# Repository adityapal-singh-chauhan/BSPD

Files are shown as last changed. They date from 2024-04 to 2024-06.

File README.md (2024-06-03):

<H1>BSPD - Brake System Plausibiltiy Device</H1>  
<BR /><H3>
A non - programmable brake, accelerator plausibility circuit.<BR />
Built for FSAE, according to Formula Bharat specs 2024.<BR /></H3>
<ul>
	<li>It feautes upper and lower thresholds for fault detection</li>
	<li>Disconnection or damage to sensor will also trigger the circuit.</li>
  <li>acc/brake_upper_trig - potentiometer sets the sensors output voltage trigger threshold.</li>
  <li>acc/brake_lower_trig - potentiometer sets the minimum volatage output of the sensor.</li>
  <li>The timing for 500ms wait and 10s shutdown can also be fine tuned.</li> 
	<li>onboard volatge regulation(input 15v - 5.5v)</li>
</ul>

BSPD

SCHEMATIC

schematic

PCB layout
PCB

LTspice sim:
all signals
red - fault signal<BR />
green - 500ms wait<BR />
blue - shutdown trigger<BR />

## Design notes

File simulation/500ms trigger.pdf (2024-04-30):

0s | 2s | 4s | 6s | 8s | 10s | 12s | 14s

0.0V

0.5V

1.0V

1.5V

2.0V

2.5V

3.0V

3.5V

4.0V

4.5V

5.0V

5.5V

V(n005)

### --- C:\Users\adity\Documents\fateh\BSPD\BSPD\comp_sim.raw ---

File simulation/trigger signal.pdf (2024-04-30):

0s | 2s | 4s | 6s | 8s | 10s | 12s | 14s

-0.5V

0.0V

0.5V

1.0V

1.5V

2.0V

2.5V

3.0V

3.5V

4.0V

4.5V

5.0V

V(n002)

### --- C:\Users\adity\Documents\fateh\BSPD\BSPD\comp_sim.raw ---

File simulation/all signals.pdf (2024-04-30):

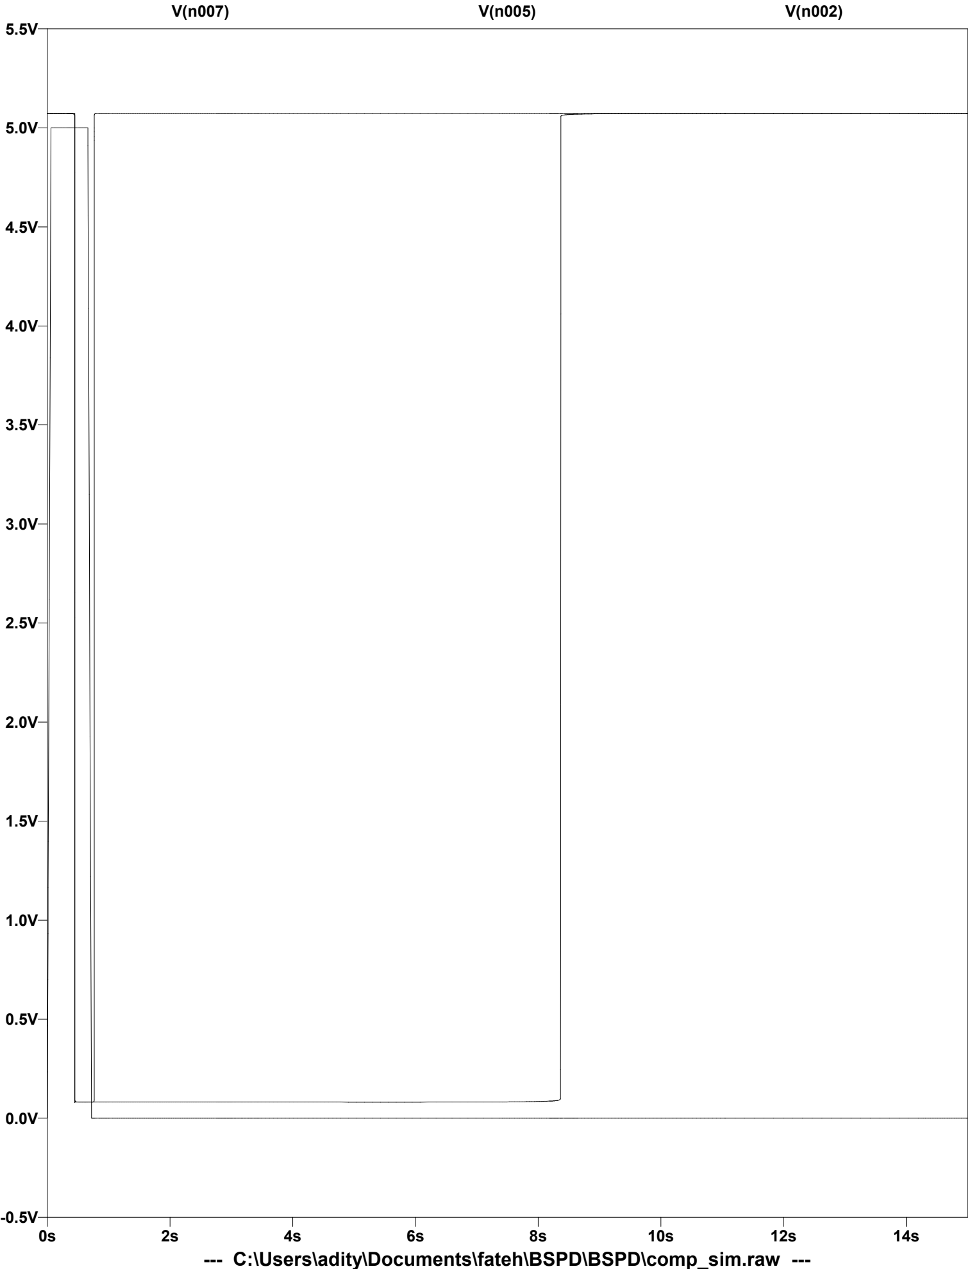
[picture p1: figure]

### --- C:\Users\adity\Documents\fateh\BSPD\BSPD\comp_sim.raw ---

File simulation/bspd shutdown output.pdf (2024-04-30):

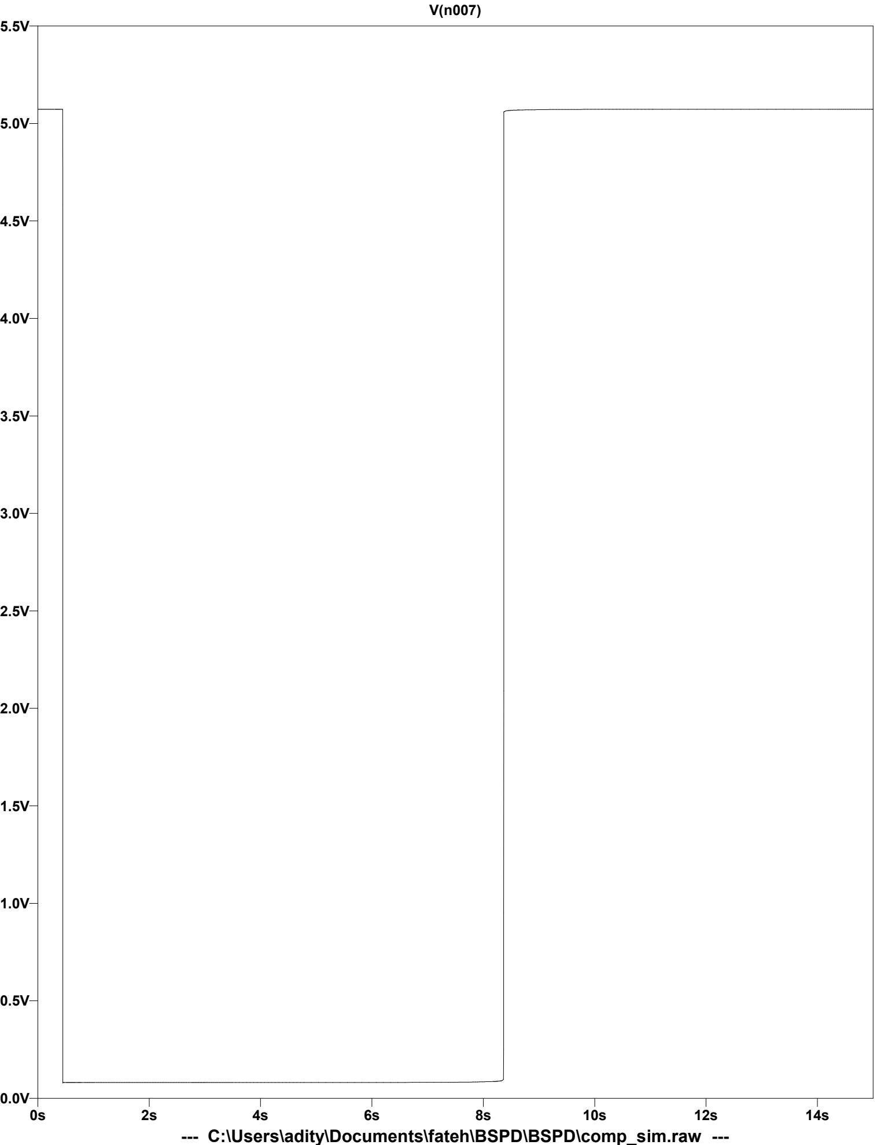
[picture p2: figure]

### --- C:\Users\adity\Documents\fateh\BSPD\BSPD\comp_sim.raw ---

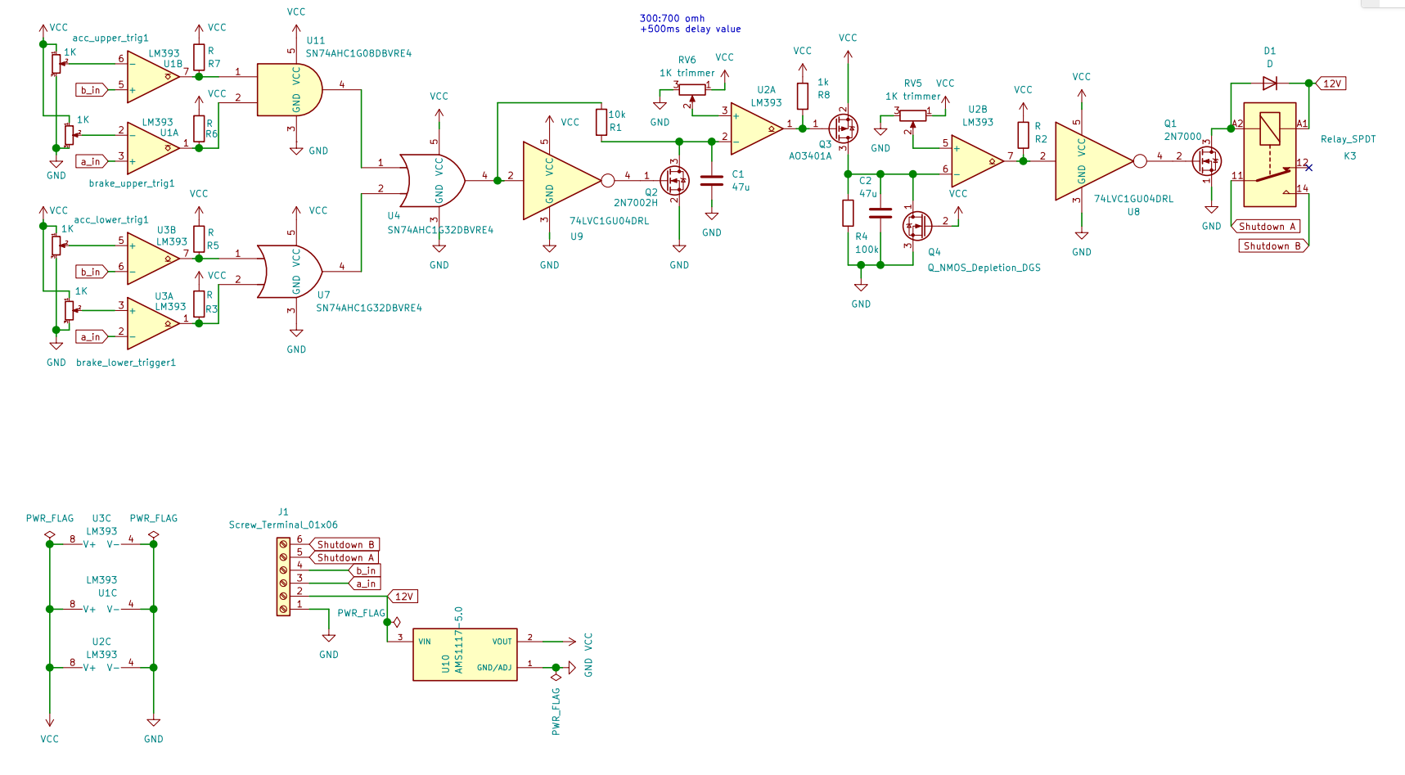
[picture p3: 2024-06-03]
schematic.png

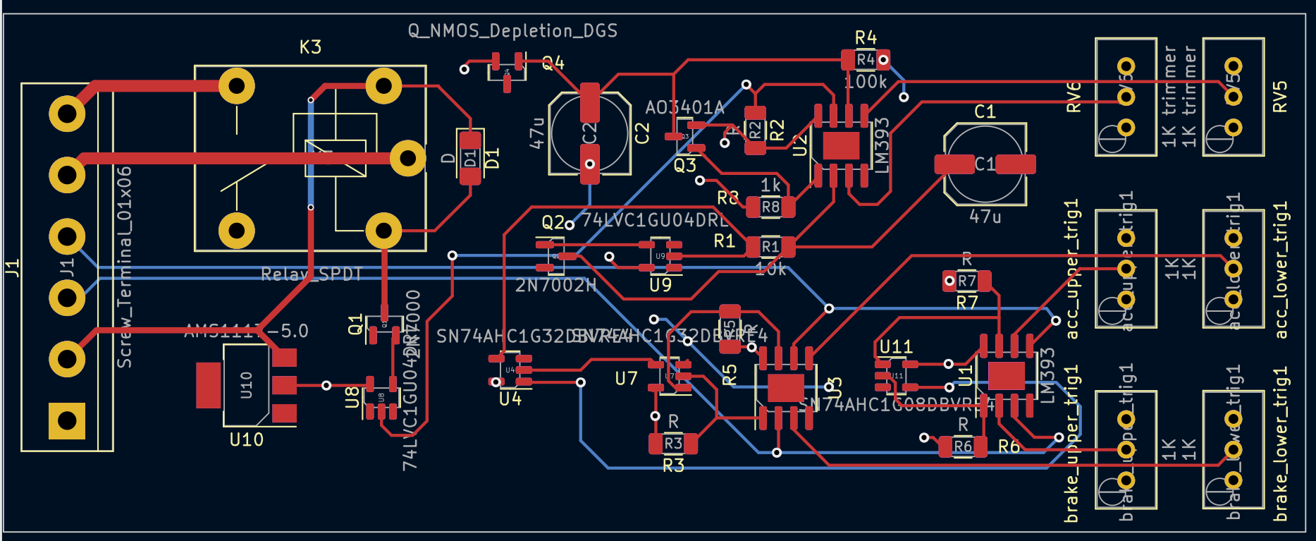
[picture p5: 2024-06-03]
PCB.png

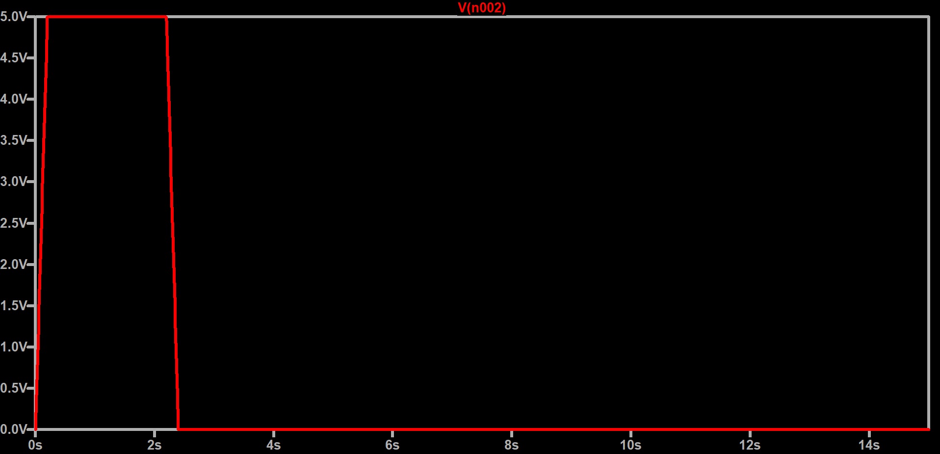
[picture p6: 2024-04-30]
simulation/trigger signal.jpg

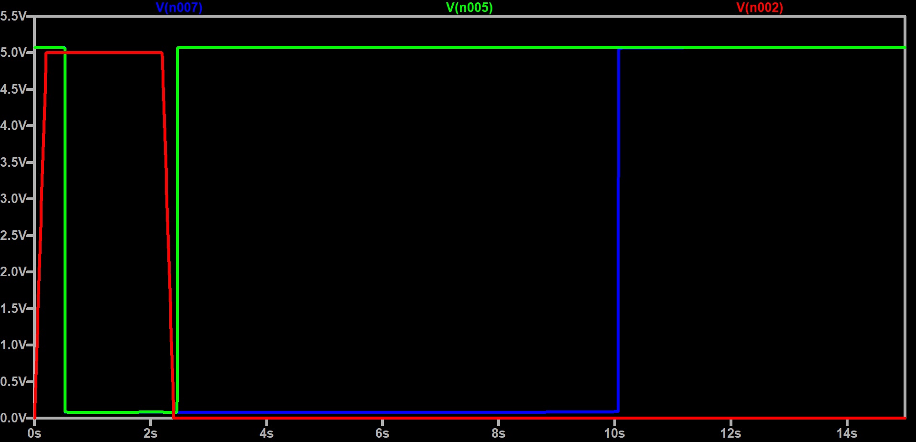
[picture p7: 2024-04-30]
simulation/all signals.jpg

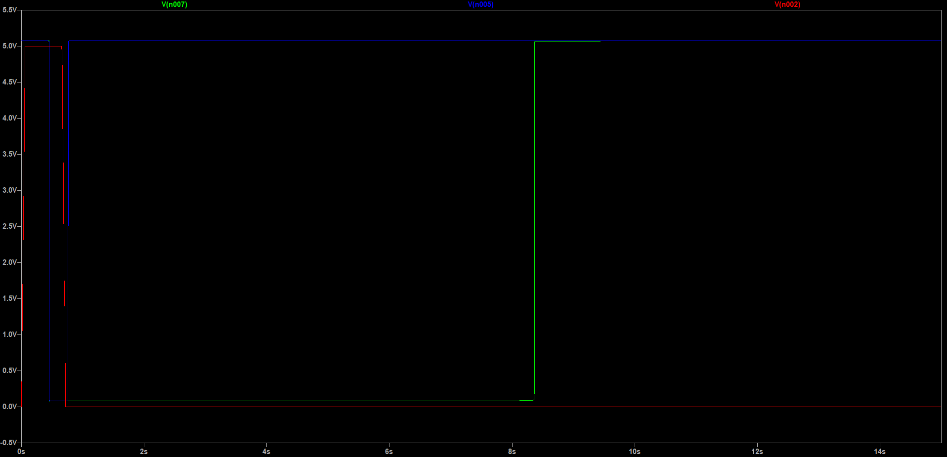
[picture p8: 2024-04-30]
simulation/all signals.png

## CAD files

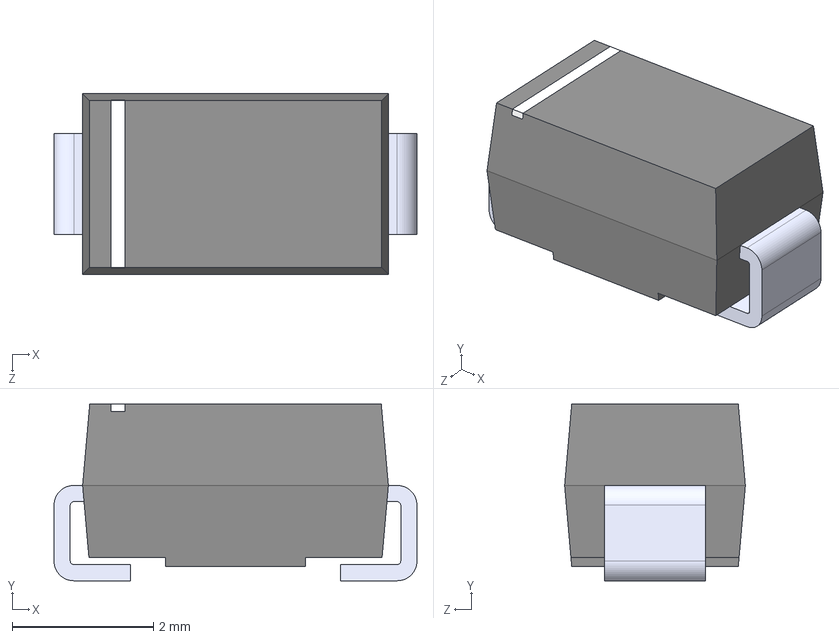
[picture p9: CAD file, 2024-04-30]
1n4007_smd/RS1G.step
5.14 x 2.50 x 2.56 mm

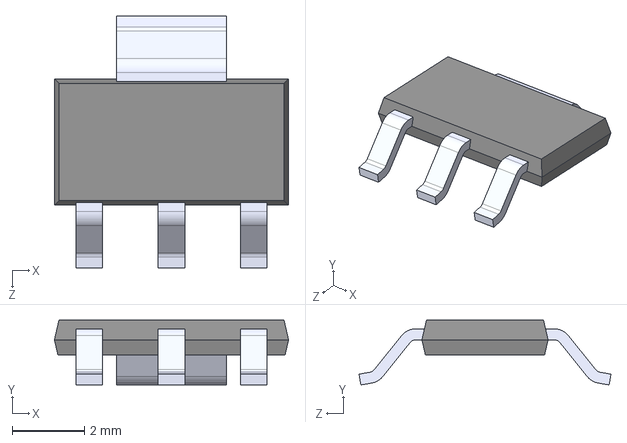
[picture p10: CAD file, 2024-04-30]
AMS1117-5.0/AMS1117-5.0.step
6.50 x 1.80 x 7.00 mm

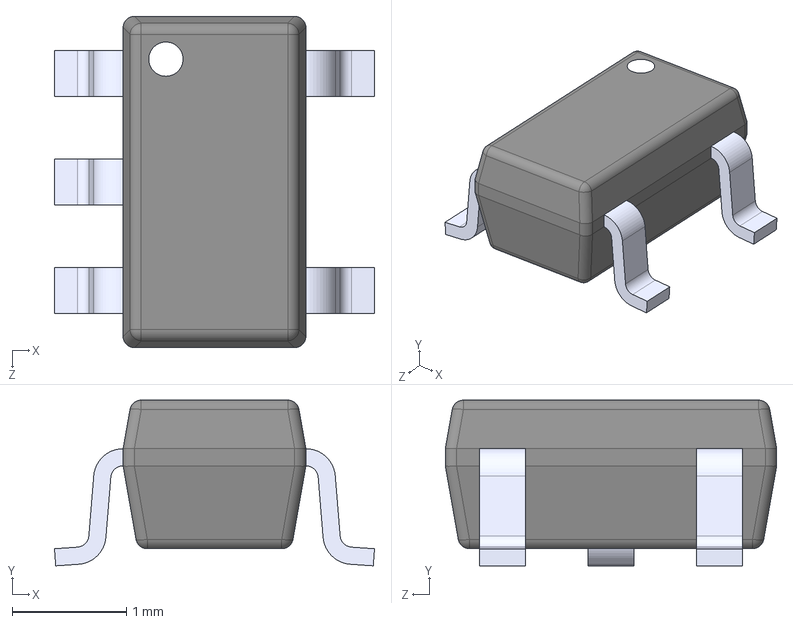
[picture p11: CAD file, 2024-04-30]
SN74AHC1G08DBVRE4/SN74AHC1G08DBVRE4.step
2.80 x 1.45 x 2.90 mm

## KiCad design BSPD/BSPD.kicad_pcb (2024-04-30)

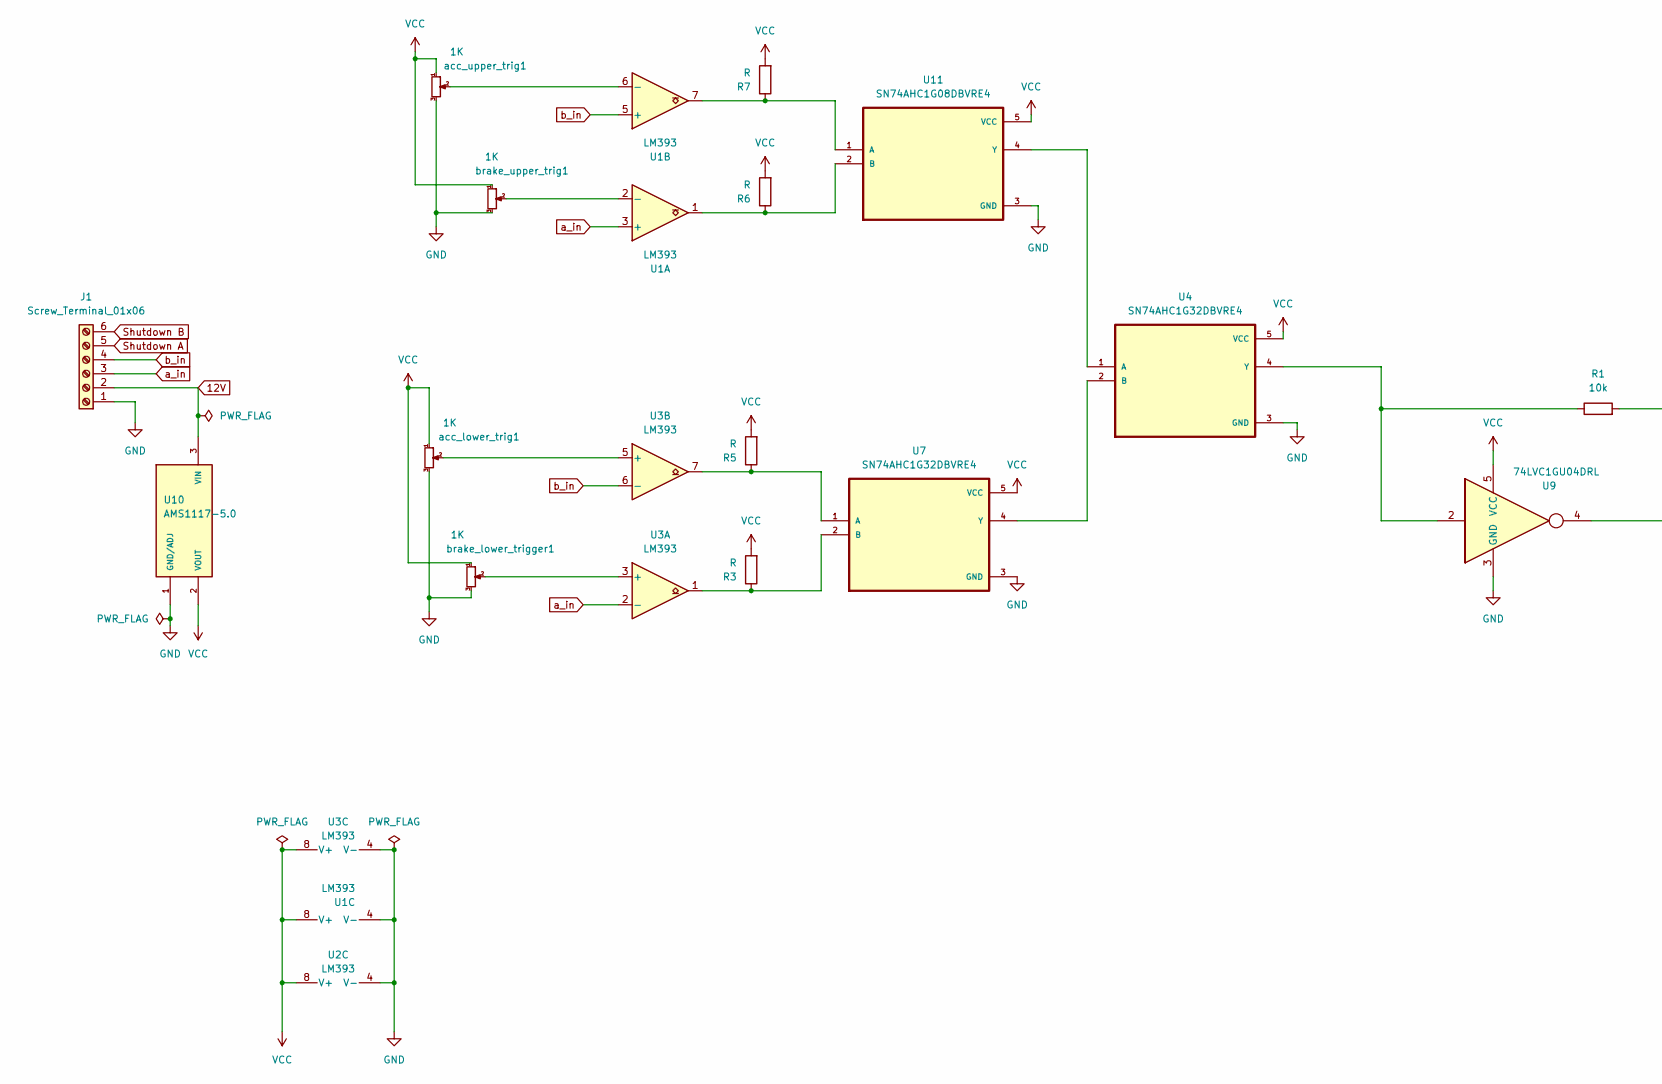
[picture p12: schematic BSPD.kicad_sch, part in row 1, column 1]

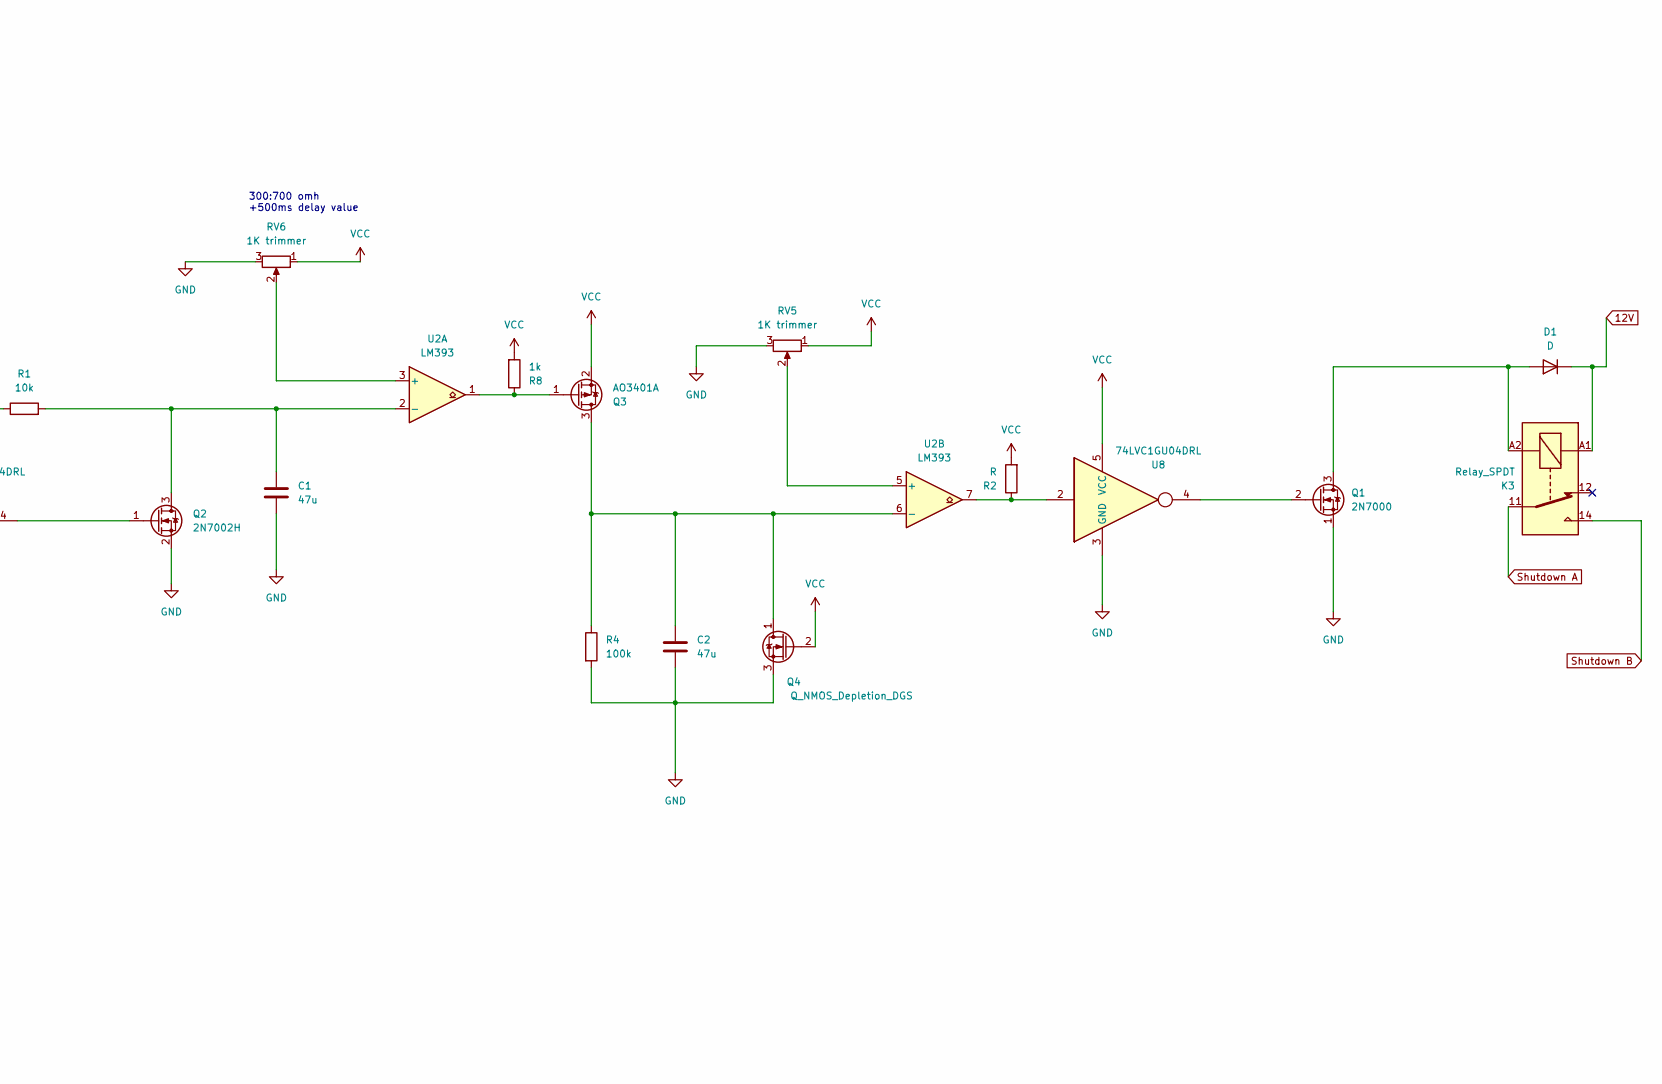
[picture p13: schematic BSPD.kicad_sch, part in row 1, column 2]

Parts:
C1, C2: 47u; C_Elec_6.3x7.7
D1: D; D_1206_3216Metric_Pad1.42x1.75mm_HandSolder
J1: Screw_Terminal_01x06; TerminalBlock_bornier-6_P5.08mm
K3: Relay_SPDT; Relay_SPDT_Finder_36.11
Q1: 2N7000; SOT-23
Q2: 2N7002H; SOT-23
Q3: AO3401A; SOT-23
Q4: Q_NMOS_Depletion_DGS; SOT-23
R1: 10k; R_1206_3216Metric
R2, R3, R5, R6, R7: R; R_1206_3216Metric
R4: 100k; R_1206_3216Metric
R8: 1k; R_1206_3216Metric
RV5, RV6: 1K trimmer; Potentiometer_Bourns_3296W_Vertical
U1, U2, U3: LM393; SOIC-8-1EP_3.9x4.9mm_P1.27mm_EP2.29x3mm
U4, U7: SN74AHC1G32DBVRE4; SOT-23-5
U8, U9: 74LVC1GU04DRL; SOT-23-5
U10: AMS1117-5.0; SOT-223; PARTREV N/A
U11: SN74AHC1G08DBVRE4; SOT-23-5
acc_lower_trig1: 1K; Potentiometer_Bourns_3296W_Vertical
acc_upper_trig1: 1K; Potentiometer_Bourns_3296W_Vertical
brake_lower_trigger1: 1K; Potentiometer_Bourns_3296W_Vertical
brake_upper_trig1: 1K; Potentiometer_Bourns_3296W_Vertical

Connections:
12V: D1.1 (K), J1.2, K3.A1, U10.3 (VIN)
GND: C1.2, C2.2, J1.1, Q1.1 (S), Q2.2 (S), Q4.3 (S), R4.2, RV5.3, RV6.3, U1.4 (V-), U2.4 (V-), U3.4 (V-), U4.3 (GND), U7.3 (GND), U8.3 (GND), U9.3 (GND), U10.1 (GND/ADJ), U11.3 (GND), acc_lower_trig1.3, acc_upper_trig1.3, brake_lower_trigger1.3, brake_upper_trig1.3; also elsewhere on the board
unnamed: D1.2 (A), K3.A2, Q1.3 (D)
unnamed: Q1.2 (G), U8.4
unnamed: C1.1, Q2.3 (D), R1.2, U2.2 (-)
unnamed: Q2.1 (G), U9.4
unnamed: C2.1, Q3.3 (D), Q4.1 (D), R4.1, U2.6 (-)
unnamed: Q3.1 (G), R8.1, U2.1
unnamed: R2.1, U2.7, U8.2
unnamed: U1.2 (-), brake_upper_trig1.2
unnamed: U1.6 (-), acc_upper_trig1.2
unnamed: RV6.2, U2.3 (+)
unnamed: RV5.2, U2.5 (+)
unnamed 13: U3.3 (+), brake_lower_trigger1.2; also elsewhere on the board
unnamed: U3.5 (+), acc_lower_trig1.2
unnamed: U4.2 (B), U7.4 (Y)
unnamed: R1.1, U4.4 (Y), U9.2
unnamed: R5.1, U3.7, U7.1 (A)
unnamed: R3.1, U3.1, U7.2 (B)
unnamed: R7.1, U1.7, U11.1 (A)
unnamed: R6.1, U1.1, U11.2 (B)
unnamed: U4.1 (A), U11.4 (Y)
Shutdown A: J1.5, K3.11
Shutdown B: J1.6, K3.14
VCC: Q3.2 (S), Q4.2 (G), R2.2, R3.2, R5.2, R6.2, R7.2, R8.2, RV5.1, RV6.1, U1.8 (V+), U2.8 (V+), U3.8 (V+), U4.5 (VCC), U7.5 (VCC), U8.5 (VCC), U9.5 (VCC), U10.2 (VOUT), U11.5 (VCC), acc_lower_trig1.1, acc_upper_trig1.1, brake_lower_trigger1.1, brake_upper_trig1.1; also elsewhere on the board
a_in: J1.3, U1.3 (+), U3.2 (-)
b_in: J1.4, U1.5 (+), U3.6 (-)

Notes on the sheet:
300:700 omh +500ms delay value

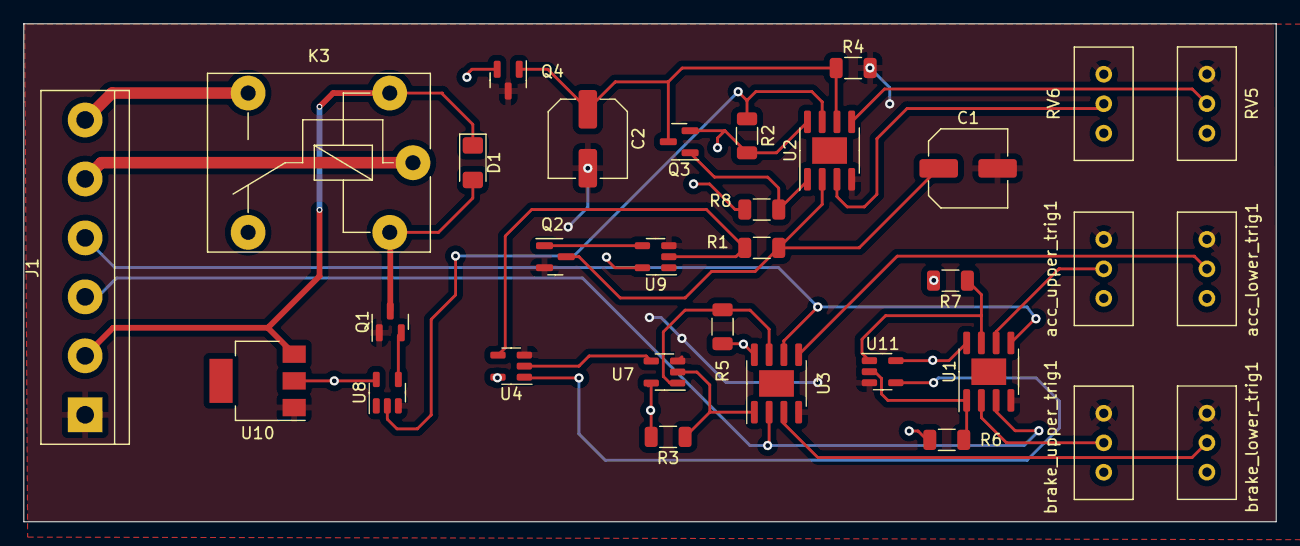
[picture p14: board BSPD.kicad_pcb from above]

Board: 2 copper layers, 107.9 x 42.9 mm, 32 parts (0 on the bottom side), 27 nets.

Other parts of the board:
brake_lower_trig1: 1K; Potentiometer_Bourns_3296W_Vertical

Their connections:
GND: brake_lower_trig1.3; also elsewhere on the board
unnamed 13: brake_lower_trig1.2; also elsewhere on the board
VCC: brake_lower_trig1.1; also elsewhere on the board
